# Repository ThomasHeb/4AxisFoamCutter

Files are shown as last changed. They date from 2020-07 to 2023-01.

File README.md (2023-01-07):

## What is new?
- Shared firmware with LaserCutter
  - tool is synchronized with grbl line execution
  - hotwire.cpp/.h is integrated in common tool.cpp/.h 
  - checkout [LaserCutter/Firmware](https://github.com/ThomasHeb/2AxisLaserCutter/tree/main/03_Firmware) for more insides
- Removed source for library modification, use provided libraries instead
- Rotary knob improved (no library needed)
- Libraries for Arduino can be downloaded directly from here (solving some issues with library updateds and conflicts with grbl)
- Added blockdiagrams for setup with Ramps 1.4 / Ramps 1.6
- Added selection guide for hotwire and power supply
- Fans are optional, if not connected, Pin 10 do not need to be cutted
- Simple postprocessor integrated in SketchUp tool Foamcutter.rb 

## What is coming next?
- Please let me know, if you have ideas or need improvements

# 4AxisFoamCutter

Arduino based CNC foam cutter with display and SD-Card.
Ruby Script for SketchUp Make 2017 to generate gcode.
Swift base post processing 

My goal was to build a foam based semi scale glider. So a lot of segments and very accurate working would have been necessary. This brought me to the idea to design the glider in SketchUp and build a 4 axis foam cutter.

The base idea ist very simple. Four independent linear axis with NEMA 17 stepper and belts. This simple system is satisfying,  because the accuracy of the belt and stepper is better than the impact of the hot wire, it's temperature and feed speed and almost no force is required to cut the foam. The only mechanical topic is to keep the hot wire stretched. Therefore I found a very good idea here on GitHub with retractable reels.

For controlling the four axis I found a solutions based on grbl 8c2 in combination with some Windows bases UIs and gcode sender. For generating the wing profiles I found some windows solutions or professional tools, but not free of charge, neither running on mac. For the fuselage I found only a professional tool. As I don't want a computer in my workshop, the gcode should be executed from a SD card, similar as my 3D printer does.  So I came to my project list:
- 4 independent axis 
- local display, SD card reader and control buttons
- Arduino based gcode handling, based on grbl 8c2 version adapted for foam cutting.
- fixed frame based on 2020 profiles, v-slot based linear actors (it is my first cnc machine, so there are much easier and better mechanical constructions, have a lock on https://www.rckeith.co.uk)
- only one power supply
- wing design with third party tools: 
  - WingHelper (I have a licence), export of gcode is possible but post process is required, I use my own post processor in MacOS, see below.
  - https://www.youtube.com/watch?v=uWO8kMGxqGU, Java based wing designer, including post processor. Exported dat file needs to be renamed to gcode-file extension. hotwire needs to be switched on manually.
  - http://www.diyrcwings.com/app/, Online wing designer, including post processor and hotwire controller. Exported file extensio  needs to be changed to .gcode
- fuselage design with SketchUp, therefore I wrote a small tool to generate gcode, see below
- post processing to adapt gcode to machine geometry for MacOS and combine multible jobs, see below

# Resources
Many thanks to all the guys giving me grad inspirations with their projects
- [rcKeith, Hot wire cutter](https://www.rckeith.co.uk/cnc-hot-wire-foam-cutter/)
- [4 axis foam cutter](https://github.com/rahulsarchive/4AxisFoamCutter)
- [4 axis foam hotwire cutter](https://www.rcgroups.com/forums/showthread.php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)

# Videos
- [Mechanic](https://youtu.be/zKdzEoycaa4)
- [Hardware](https://youtu.be/xaXfXsz1NG8)
- [Firmware](https://youtu.be/fht_X7mQ-qg)
- [Functions](https://youtu.be/SWv79BavgKs)
- [Working with SketchUp Part 1](https://youtu.be/MZSXp2stBLk)
- [Working with SketchUp Part 2](https://youtu.be/SIh3zpsxGX4)
- [Working with SketchUp Part 3](https://youtu.be/uU0HhuviuLE)
- [Working with SketchUp Part 4](https://youtu.be/WJ8nHyDqIhs)
- [Post processing Basics](https://youtu.be/D0ZCudA9wv8)
- [Post processing merging shapes](https://youtu.be/Z-096iua6jk)
- [Feed speed optimization with preprocessor](https://youtu.be/2PEHMFtozhw)
- [Post processing code insides Part 1](https://youtu.be/n6ZeKAKcKlE)
- [Post processing code insides Part 2](https://youtu.be/POwDu0zc9eI)

# Mechanics
- 4x linear v-slot actuator with NEMA 17
- 2020 profiles, screws, nuts
- nichrome wire
- 2-4x retractable reel 

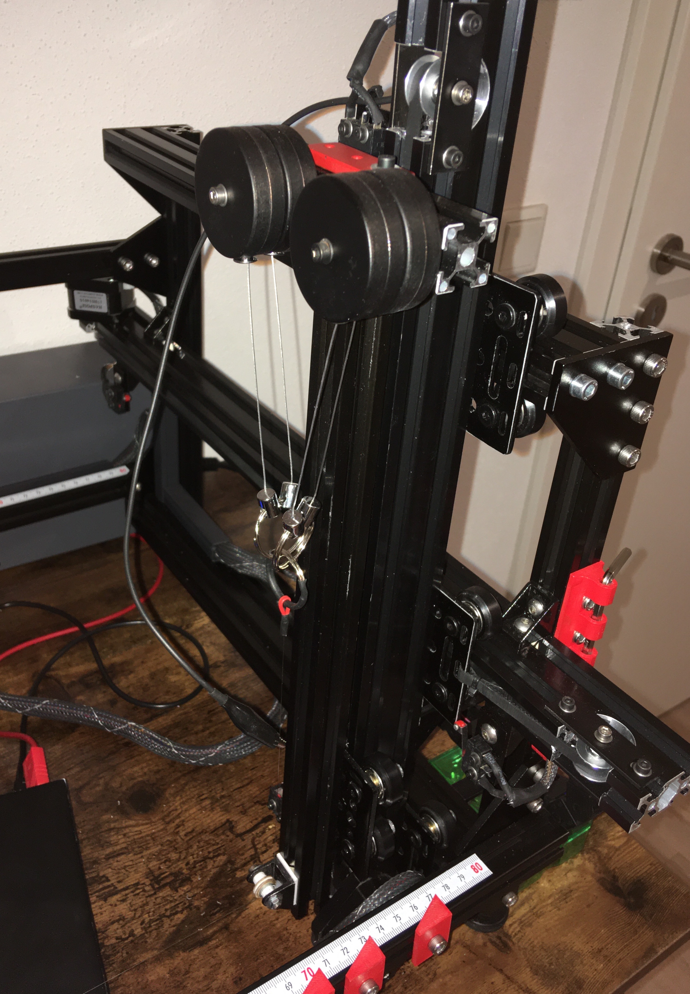
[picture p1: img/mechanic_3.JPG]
mechanic_3

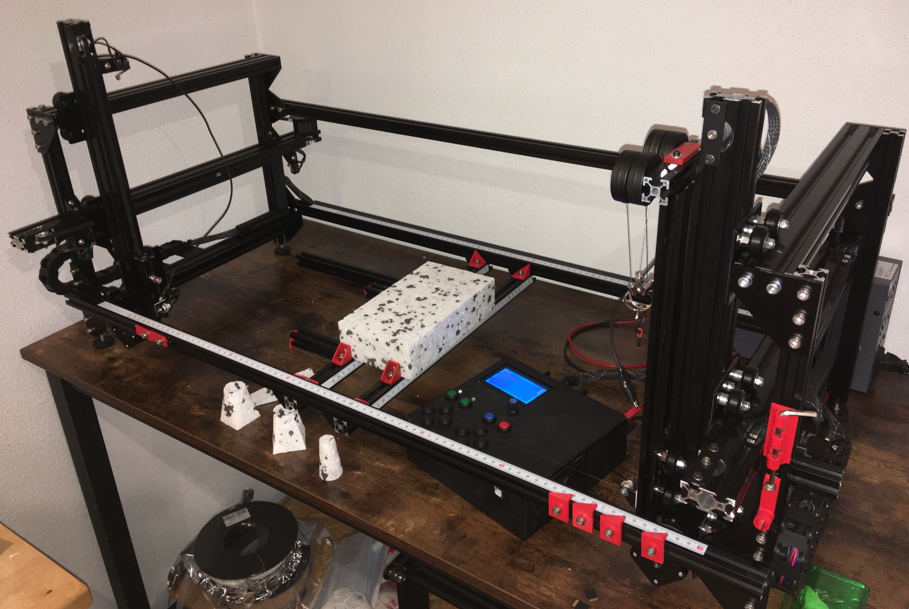
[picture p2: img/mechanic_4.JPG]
mechanic_4


[Video: Mechanic](https://youtu.be/zKdzEoycaa4)

# Hardware
- Arduino Mega 2560
- 128x64 LCD Display / SD card reader from RepRap with connector to Ramps 1.4 or 1.6
- Ramps 1.4 or 1.6
- 4x stepper driver A4988 (on E0, E1, Y, Z socket 0f ramps)
- 8x micro switch NC as limit switch
- 4x 100nF capacitor
- 12 buttons NO
- 2x LED + resistor 2k2
- DC-DC converter (in: > 30V, out 12V, app. 2A), not for Ramps 1.6
- optional: fans 12V
- wire / connector

Most of it is plugged together straight forward. A detailed list is included in the foamcutter.ino file.

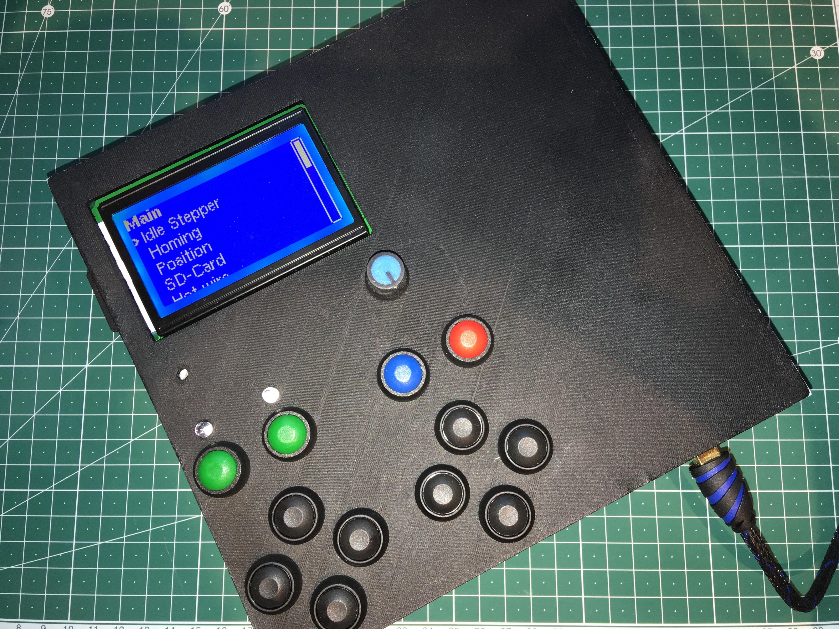
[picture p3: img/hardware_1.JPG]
hardware_1

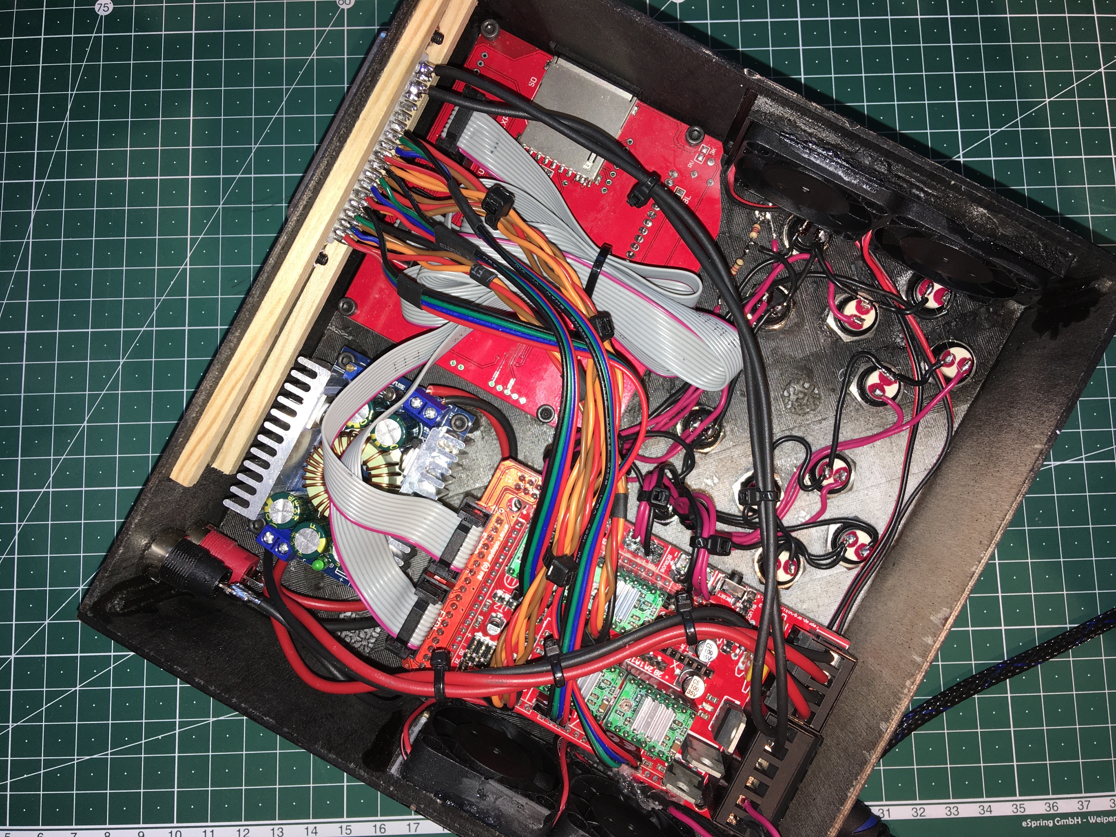
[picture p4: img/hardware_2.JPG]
hardware_2


### Blockdiagram for Ramps 1.4
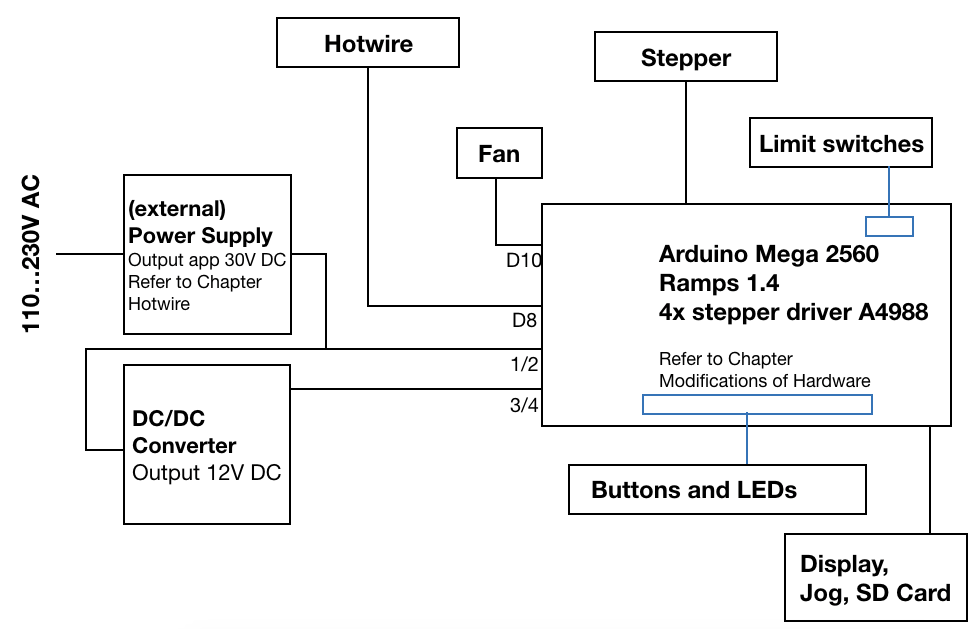
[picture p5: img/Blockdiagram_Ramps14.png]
blockdiagram_ramps14


A power supply is used with up to max 35V (limit of on board MOSFET on the Ramps) to supply the hotwire and the DC/DC converter. Refer to chapter Hotwire for voltage / power adjustment and selection of the right power supply.
The DC/DC converter supplys 12V DC to the Ramps, display, stepper and Arduino. I would not recommend more than 12V DC, because on the Arduino a linear voltage regulator is used to generate 5V DC and this can be easily over powered / heated, when input voltage is to high.
App. 30W are needed for Ramps, display, stepper and Arduino. In addition required power for the fans. I am using this [DC/DC converter](https://www.amazon.de/gp/product/B00HV4EPG8/ref=ppx_yo_dt_b_asin_title_o01_s01?ie=UTF8&psc=1), powering 4 small fans.
To select the right power supply, you need to keep estimate the power for the hotwire (see chapter Hotwire), power for Arduino, Display,... (app 30W) and the fans (20W for the small ones I am using), see chapter Power supply.
In my setup, nothing is getting hot, so I do not switch the fans on.... you do not really need fans.
Please check your power supply, if cooling is required. Please keep all standards and safety topics in mind, when handling with high voltage on power supply, best is to contact an authorised specialist.
A detailed list of all connections/wiring is included in the foamcutter.ino file.

Advantage:
- separate voltage for hotwire, helps to select best resistance wire, see chapter Hotwire. Especially with a small diameter: Higher hotwire voltage allows to have less current in the hotwire, select thiner wires with a higher wire resistance.

Disadvantage:
- additional hardware (DC/DC converter) needed, app 10 EUR 

### Blockdiagram for Ramps 1.6
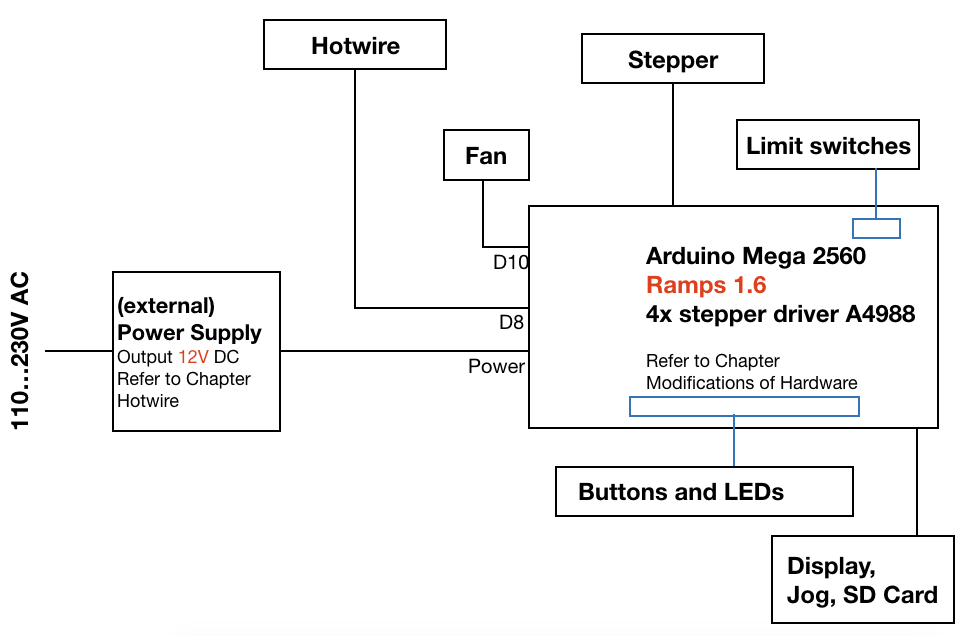
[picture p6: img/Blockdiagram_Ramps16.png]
blockdiagram_ramps16


A power supply with 12V DC output is used, because on the Arduino a linear voltage regulator is used to generate 5V DC and this can be easily over powered / heated, when input voltage is to high.
App. 30W are needed for Ramps, display, stepper and Arduino. In addition required power for the fans and the hotwire (see chapter Hotwire and Power supply).
I did not build a version with Ramps 1.6, but checking all the data sheets and diagrams, there should be no fan required for additional cooling of the Ramps board itself.
Please check your power supply, if cooling is required. Please keep all standards and safety topics in mind, when handling with high voltage on power supply, best is to contact an authorised specialist.
A detailed list of all connections/wiring is included in the foamcutter.ino file.

Advantage:
- no DC/DC converter is needed
- less wiring

Disadvantage:
- lower voltage for hotwire requires higher current  to achieve power for cutting. hotwire is getting thicker.

### Other Boards
Other boards may works, as long as they are based on the same or similar pin connection as the Ramps does. See Issues and search for MKS Board.

### Hotwire
Selecting the right hotwire is a bit tricky
I am cutting XPS foam with a very slow feed rate (100mm/min) for good results.
On my machine I have 20 W/m (watt per meter) to achieve good results. For calculation I would recommend to use 25 W/m (fine tuning can be done in power setting parameter).

Get the length L of your hotwire. Keep in mind that you have diagonal traveling of the hotwire, so the wire length is more than the machine width.
Get the Input voltage Ui for the hotwire (Ramps 1.4: app 30V (max 35V) / Ramps 1.6: 12V)
Calculate the total wire resistance Rtotal and the wire resistance per feet Rf

- Ptotal = L x 25 W/m
- Rtotal = Ui x Ui / Ptotal
- Rf = Rtotal / (L (in m) x 3,28)

The higher the input voltage Ui is, the higher is Rf, the lower the current through the wire and the MOSFET on the ramps. the MOSFET will stay cooler and most important, you can select thiner wires.
Now you can find the best fitting wire by checking the wire resistance per feet (Ohm/feet).

Example:
Total Hotwire length L = 0,9m. power supply works with output voltage of 30V (= Ui).
Ptotal = 0,9 x 25W/m = 22,5 W
Rtotal = 30 x 30 / 22,5 = 40 Ohm
Rf = 40 / (0,9 x 3,28) = 13 Ohm per feet
I would go for 
Kanthal A1 32G with 13,1 Ohm/feet [Link](https://www.amazon.com/-/de/dp/B07CHTFJ3J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)

Due to the calculation with 25W/m you will need to reduce power setting parameter for hotwire a bit to app 90…90%

Next step is to fine tune all your settings
- Go to the hotwire menu , select manual and start with a low power setting.
- Put some foam on it... the foam should not be cut.
- increase power setting until the foam is cut without putting force/weight on it. this is the setting for slow cutting speed (app 100 mm/min). Check out the [video](https://github.com/ThomasHeb/4AxisFoamCutter/files/5382446/IMG_4588.mov.zip).
- Put this setting into the parameter ($5 = feed speed and $27 = hotwire power is stored automatically from your last manual setting).

If your wire is not getting hot enough:
- increase input voltage (only with ramps 1.4: 28V >>> 30V)
- reduce wire length (put the crocodile connections closer together)
- chose a wire with a lower resistance .... thicker wire ;(

If your wire is getting much too hot / cutting is starting below 50% powersetting:
- there is no urgent need to change something
- reduce the voltage a bit. don't go below 10V to have enough power for the stepper
- increase wire length
- choose a wire with higher resistance >>> smaller diameter ;)

Start fine-tuning again until you are happy with the result.

### Power Supply
Selecting the right power supply is mainly based on four factors
- input voltage, select this according your region and local 
- choosing a power supply to integrate in the foam cutter or as a separate power supply (i.e. laboratory power supply)
- output voltage 12V DC or up to 35V DC. I would not recommend to use more than 60V DC because of risk of electrical shock)
- required power: 30W for Arduino, Display, Stepper + Fans (I use small 12V DC fans with total 20W) + hotwire Ptotal (see chapter Hotwire)

Please keep all standards and safety topics in mind, when handling with high voltage on power supply, best is to contact an authorised specialist.

### Operation without buttons, leds and limit switches (minimum operation setup)
There are some sets available for 3D printer, including Arduino Mega, Ramps 1.4, 128x64 Display with SD card reader and stepper driver 4988. The firmware can be configured to operate especially with this hardware setup, without buttons, led and limit switches. The usability is limited, but almost no soldering is needed.
To use this setup, simply skip all steps related to limit switches, buttons and leds. the local button on the display is used as back button, all other operations can be handled with the jog.
- set USE_LIMIT_SWITCHES to 0 in config.h to disable the limit switches 
- set USE_BUTTONS to 0 in config.h to disable the buttons and leds 

### Modifications of Hardware:
- cut-off Arduino PIN 10 on Ramps (just cut of the pin-header on the Ramps) (not required if no fan is connected) 
- connect Arduino Pin 7 on Ramps to Socket off pin 10 (not required if no fan is connected) 
- to reduce EMC connect 100 nF between S and - close to Ramps for limit switches / end stops
- to reduce EMC connect 100 nF between D63 and GND directly on Ramps pin header for AUX-2 (not required if stopp button is close to ramps) 

### How to start:
The Arduino and the Ramps board are working without the stepper driver or motors or buttons,…. so only the limit switches should be disabled by setting 4 jumpers to the S and - Pin for X-/X+/Y-/Y+ an the Ramps. After downloading the firmware with the Arduino IDE, please use the Serial Monitor (Baudrate 115200) with the [grbl commands](https://github.com/gnea/grbl/wiki/Grbl-v1.1-Commands) to disable hard limits and homing cycle in the parameter. After testing all axis, SD card, …, you can activate the limit switches (hard limits) and the homing cycle again. If you are not disabling the limit switches, you may get a hard error, which blocks all communication to the Arduino (not required, if USE_LIMIT_SWITCHES is set to 0). After that you should 
- connect the display to the Ramps
- connect the Arduino with the USB
- load the firmware and check if you get a welcome screen
- add the buttons and LEDs to the Ramps (not required, if USE_BUTTONS is set to 0)
- calculate the steps per mm and set the microstepps according with the jumpers (I use belt and pully with 80 steps / mm) 
- add the stepper driver to the Ramps
- adjust the driver [link](https://www.makerguides.com/a4988-stepper-motor-driver-arduino-tutorial/)
- connect 12V DC to Ramps 3/4
- add a stepper motor and test operation

[Video: Hardware](https://youtu.be/xaXfXsz1NG8)

# Firmware
The firmware is based on the grbl version 8c2 modified for foam cutter, a modified version of U8G2 library for the display and SdFat with no changes.

Links to the original 
- [grbl 8c2 foam](https://www.rcgroups.com/forums/showthread.php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)
- [U8G2 Lib by Oli Kraus, tested with version 2.27.6](https://github.com/olikraus/u8g2)
- [SdFat by Bill Greiman, tested with version 1.2.3](https://github.com/greiman/SdFat)

Many thanks to you, for writing and sharing this fantastic code.
The firmware is a common project with [2 Axis Laser Cutter](https://github.com/ThomasHeb/2AxisLaserCutter).
Please use defines in config.h to select the right funtionality.

### How to install:
- Download the foamcutter firmware
- Download the libraries directly from this github (recommended):
  /03_Firmware/libraries and store in your ../Arduino/libraries/ folder (prefered, because updates of the original libraries may cause problems with grbl)
- Select Version FOAM_CUTTER in config.h

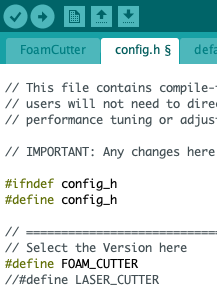
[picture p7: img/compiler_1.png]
compiler_1
  
  
### Changes within the library U8G2 - only for information:
Grbl uses almost all resources of the Arduino to control the stepper within an accurate timing. So the standard approach of Arduino is not working any more, because some resources are not available anymore for the Arduino framework. Within the U8G2 I use a software driven SPI on pin D50 to D52. The only thing I needed to change, was the required delay within the SPI. Therefore I changed the delay function to the grbl supported delay function.

### LCD, SD card and buttons, ….
The LCD display and the buttons are controlled inside the lcd.h and lcd.cpp. Buttons are read within the lcd_process(), from where all processing functions of the sub menus are called.
Functions within the sub menus, which are related to cnc functionality are called as if they would have been called via UART/USB. So you will get an ok over the UART/USB for a local called cnc command, too. The firmware can still be controlled with gcode sender tools via the UART/USB.
SD card is processed inside lcd.cpp and lcd_process(), too. Processing of the SD card is handled with a state machine, which reads the selected file char by char, similar as reading the UART. 
During processing a file from SD card, buttons are ignored, operation can only be stopped with an IRQ of the limit switches or the e-stop.
Fan can only be controlled locally on the display. Hotwire can be controlled via the display and with the gcode commands M3/4 for on and M5 for off and Sxxx (0…100) for regulating the power in %.

Please have a lock at the parameters (command $$ over Serial Monitor)

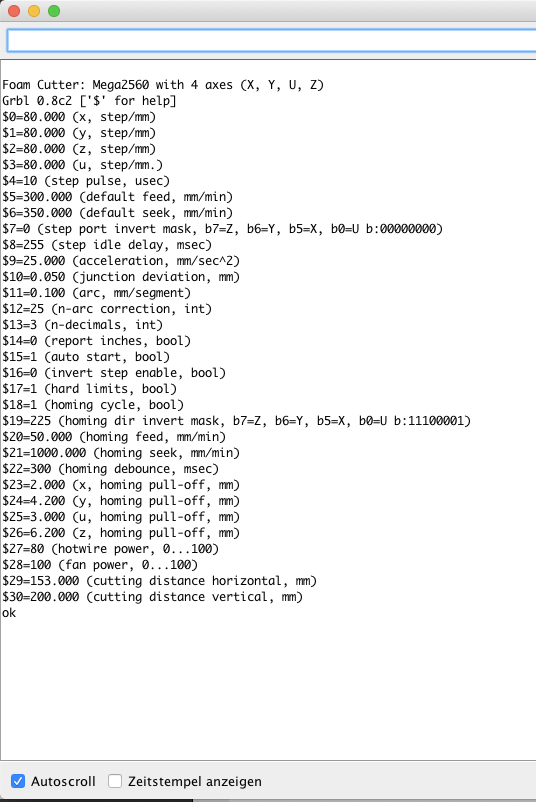
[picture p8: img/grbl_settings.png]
grbl settings


[Video Firmware](https://youtu.be/fht_X7mQ-qg)

### Functions on local display / buttons
- e-stop: IRQ based local stop, this does not match the requirements of any safety standard (not available, if USE_BUTTONS is set to 0)
- Idle stepper
- Homing (not available, if USE_BUTTONS is set to 0)
  - homing including pull-off
  - set current position as new pull off position: This function is used to travel from limit switches to machine zero position. Adjust the position with the position menu
- Position
  - adjust each axis independent
  - set or travel to a temporary home position
  - set or travel to a temporary zero position
  - 8 buttons to control the movements (not available, if USE_BUTTONS is set to 0)
  - switch speed between feed and homing seek for fast traveling (selected homing seek speed is indicated by LED
- SD-Card
  - read file list from SD-Card (only with defined file extensions (config.h), only from root directory, keep filenames short)
  - valid gcode file extensions: .nc, .gcode (you may change the file extension to oneof these)
  - execute a file from the SD-Card
  - visualise the progress (bytes read and send to gcode processing, not bytes really executed)
- Hotwire
  - switch on/off or change the power in %. New value is stored in the eeprom
  - switch on/off with button (not available, if USE_BUTTONS is set to 0)
  - indicate status with LED
- Feed speed 
  - select the feed speed
  - new value is stored in the eeprom
  - if gcode includes feed rates, gcode values are used.
  - adjust in big steps with Y- / Y+ buttons (not available, if USE_BUTTONS is set to 0)
- Slicing (previous function name: Cutting)
  - this functions allows horizontal or vertical slicing w/o gcode
  - select the slicing direction with the 8 buttons for the axis (not available, if USE_BUTTONS is set to 0, direction is selected with jog)
  - define the maximum x/y travel for slicing (use position menue)
  - executes a cut by preheating the hotwire for 5 seconds
  - move back to starting position of the slice with seek-speed
- Fan
  - switch on/off or change the power in %. New value is stored in the eeprom
- The firmware can still be controlled with gcode sender tools via the UART/USB 

- [Video: Functions](https://youtu.be/SWv79BavgKs)

### How to start:
Please refer to grbl documentation for parameter settings and first steps. A good point to start is to:
- disable limit switches and homing cycle (not required, if USE_LIMIT_SWITCHES is set to 0)
- set the steps per mm for each axis
- check the direction and adjust with "step port invert mask"
- check travel distances and optimize
- activate homing cycle and check directions and adjust with "homing dir invert mask" (not required, if USE_LIMIT_SWITCHES is set to 0)
- a good setting to start is feedrate 300 mm/min, hotwire 80% on 30V DC for 75 cm hotwire

# Working with SketchUp

I use SketchUp for generating the stl-files for my 3D printed parts. I would love to use the easy handling for creating fuselages. I searched the web and found only one hotwire related tool, which is not supported any more. so I decided to write a small tool by myself. This allowas you to generare G90 (abolute positioning) coordinates of combinded edges. Currently I use only linear extrapolation in combination with my post processor. The results are good.

### What you need
- SketchUp (I am Using SketchUp Make 2017)
- Ruby Code Editor
- CurviLoft
- Download foamcutter.rb from the code section

### Functionality and usage of foamcutter.rb
Open the ruby code editor first and load and execute the foamcutter.rb. This adds 4 menus to the PlugIn menu. 
- FoamCutter Settings: you can define some general settings, like inch/mm, used decimals.
- FoamCutter Import how-file: Import profiles from Wing Helper
- FoamCutter Tool: Generates gcode for 2 paths and exports it. The paths it self use the green (x and u) and blue (y and z) axis. Positioning along the red axis does not matter. See tutorial video "Working with SketchUp Part 1-3"
- FoamCutter Tool PP: Generates gcode for the left and the right axis of the foamcutter, this includes a simple post processing. See tutorial video "Working with SketchUp Part 4"

The algorithm searches all related points to an edge. It follows two routes
### 1: go up first (Y/Z +)
### 2: go back first (X/U -)
It uses all edges only once. If you reach a dead end, you may use the third dimension (supporting path) do open up new paths/edges - please keep the rules in mind.

Both paths should have the same number of points and edges. To go for that with more complex objects, it is a good way to use CurviLoft
- create your objects
- use CurviLoft to generate the surface/area between the objects. 
- select to show the related edges between the objects (connection lines)
- split these connection lines (ungroup)
- select and group the objects (otherwise the object is not splittet in points)
- delete the connection lines
- use foamcutter tool
- select first and second edge
- save the file
- do the post processing if required

### Check out the tutorial video
- [Working with SketchUp Part 1](https://youtu.be/MZSXp2stBLk)
- [Working with SketchUp Part 2](https://youtu.be/SIh3zpsxGX4)
- [Working with SketchUp Part 3](https://youtu.be/uU0HhuviuLE)
- [Working with SketchUp Part 4](https://youtu.be/WJ8nHyDqIhs)

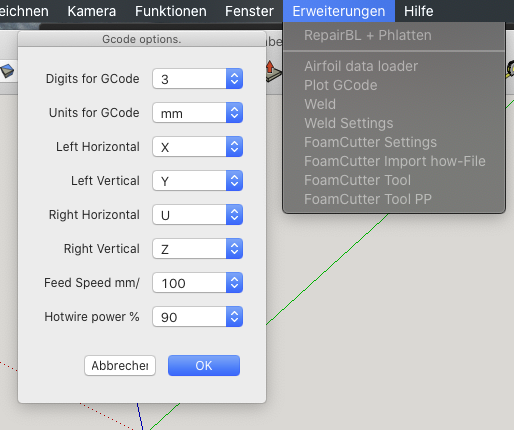
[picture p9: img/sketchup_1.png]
sketchup_1

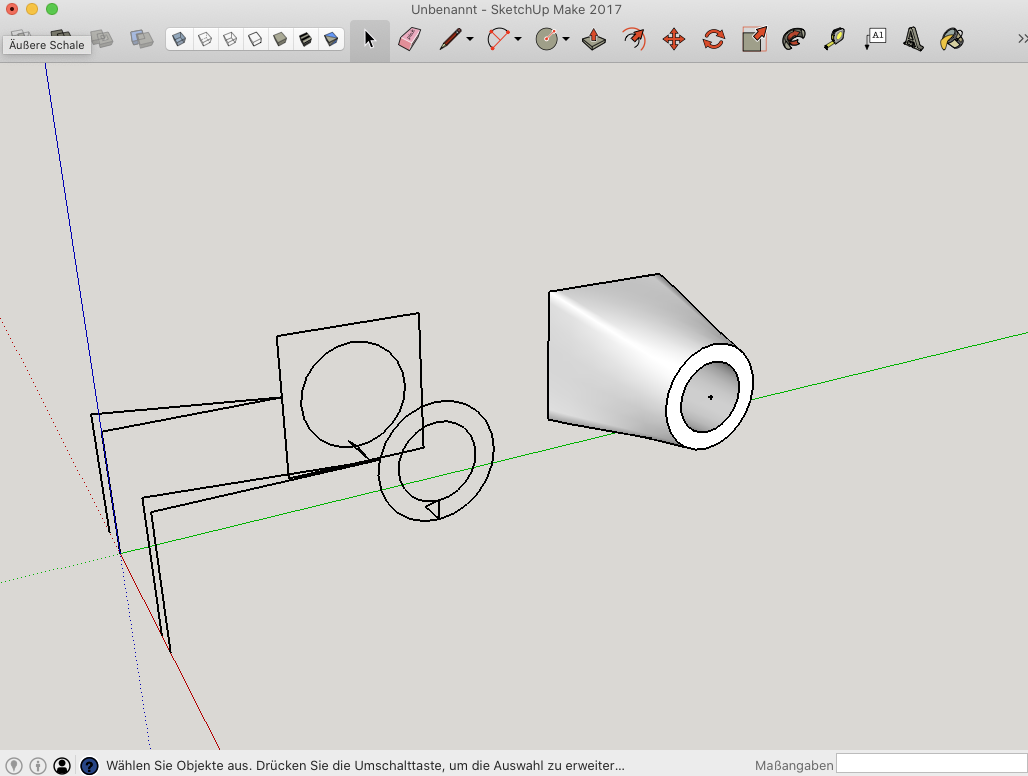
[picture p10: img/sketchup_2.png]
sketchup_2


# Post processing
Designing the shape of a wing or a fuselage requires in most times an additional step to tell the machine / foam cutter how to produce it. This step is called post processing. It allows you to generate machine executable or interpretable code (gcode) and add machine, tool and material specific information (hot wire temperature, travel speed, position of foam block, …). I wrote a pice of code, do adopt my SketchUp files and my WingHelper Designs to my foam cutter. The code is written in swift for macOS, but the basic ideas can be easily adopted to other languages. All post processing functions are bundled in the class FCalc (FCalc.swift). Interfacing is handled with key to access the values and the labels/descriptions to the values. The values itself are exchanged as Strings, because most of them are changed by user, so all type checking stuff is integrated in FCalc, too. Detailed interface description is available in FCalc.swift.

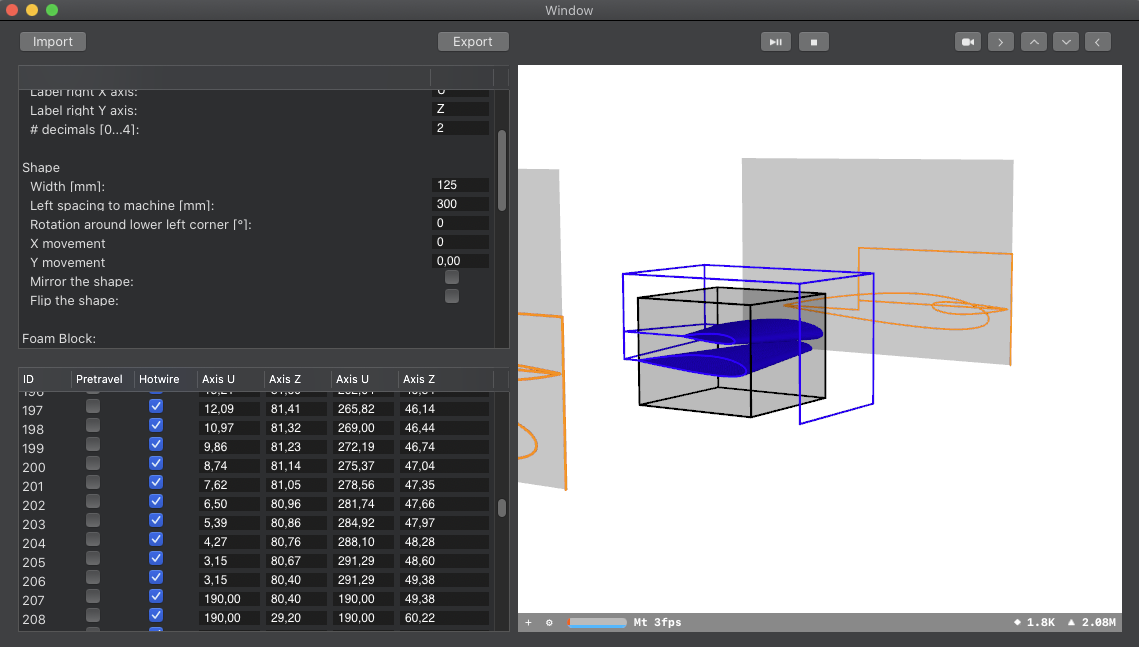
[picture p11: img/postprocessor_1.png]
postprocessor_1


### Overview of functions
- Import shapes from gcode, nc, SkechUp foamcutter.rb, Winghelper how, fcf-projects
- Export to gcode
- Load/Save projects as fcf file
- Move and rotate and mirror the shape 
- Move and rotate the foam block
- Calculates the movement of the axis
- Speed optimisation, to keep average speed at the edges of the shape close to target feed speed
- Merging of different shapes into one cutting job
- 3D preview and simulation of axis, shape and foam block

### Check out the tutorial video
- [Basics](https://youtu.be/D0ZCudA9wv8)
- [Merging shapes](https://youtu.be/Z-096iua6jk)

### Settings
- All settings have a unique ID (see SettingsTableKey for all values) for access
- Reading a setting:
  - dataTypeForKey(_ key: SettingsTableKey) -> DataType              
    the Datatype of the setting for correct visualisation/layout
  - labelForKey(_ key: SettingsTableKey) -> String                   
    the label for the setting
  - valueForKey(_ key: SettingsTableKey) -> String                   
    the value itself for the key as formatted string
- Writing:
  - isEditableForKey(_ key: SettingsTableKey) -> Bool                
    indicates wheather this type is editable
  - isValueValid(_ key: SettingsTableKey, value: String?) -> Bool    
    a string can be tested, if it is acceptable for this setting
  - valueForKey(_ key: SettingsTableKey, value: String?)             
    writes a string to the setting
- Usage: Generate an array of SettingsTableKey-values to be displayed and catch the content with the functions above
- All is handled with strings, so no need of type conversion

### Import a file / export GCode
- Supported filetypes;
  - gcode, nc: simple gcode wit G00/G0, G01, G1, G90, G91, ...
  - how: Winghelper ICE export with absolute coordinates
  - fcf: Foam Cuter File (project) previously saved
  - importShapeFromFile(_ file: String) -> Int       
    =  0 if ok / != 0 if not ok
- Save a file in gcode format
  exportGCodeToFile(_ file: String) -> Int         
  =  0 if ok / != 0 if not ok

###  Callbacks (FCalcCallback):
- updateSettingsTableView()  
  called, wenn the table for the settings needs to be updated
- updatePositionsTableView(_ atIndex: Int?)                                 
  called, wenn the table for the positions needs to be updated
- updatePreview(_ node: SCNNode)  
  called, whenn the Graph is updated, check if Node is already linked

###  Changing Values / Coordinates:
- optional, see FCalc.swift

###  Videos explaining some code insides:
- [Part 1](https://youtu.be/n6ZeKAKcKlE)
- [Part 2](https://youtu.be/POwDu0zc9eI)

# Samples
See folder 99_sample in the code section:
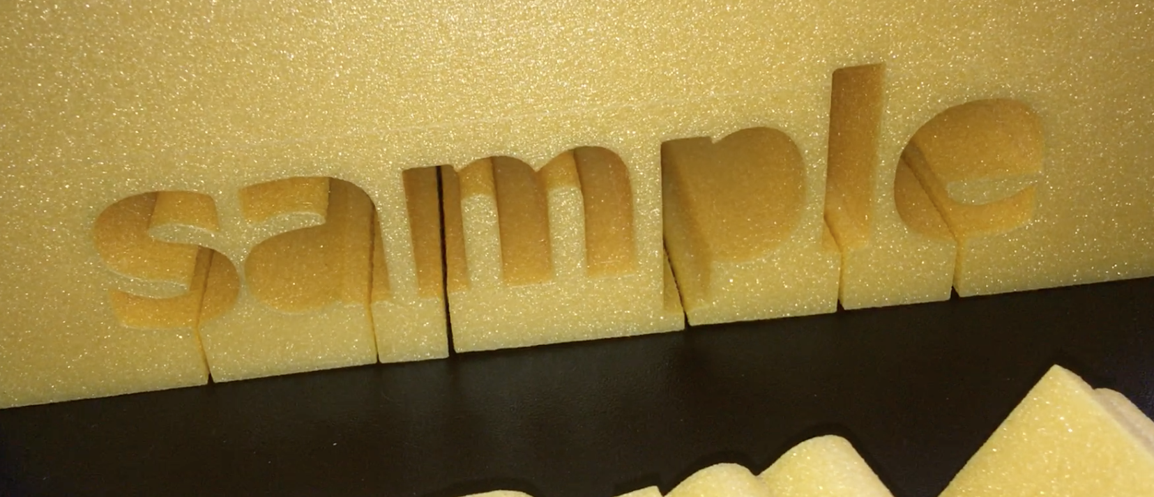
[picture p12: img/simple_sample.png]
simple_sample

- sample_1.gcode is the export file from foamcutter.rb (SketchUp) 
- sample_2.gcode header and commandes were modified manually with text-editor
- sample_pp.gcode is generated with post processor

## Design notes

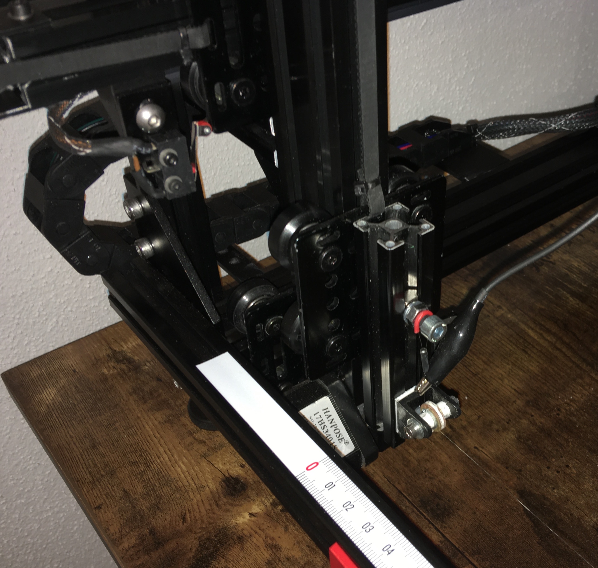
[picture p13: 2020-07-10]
img/mechanic_2.JPG

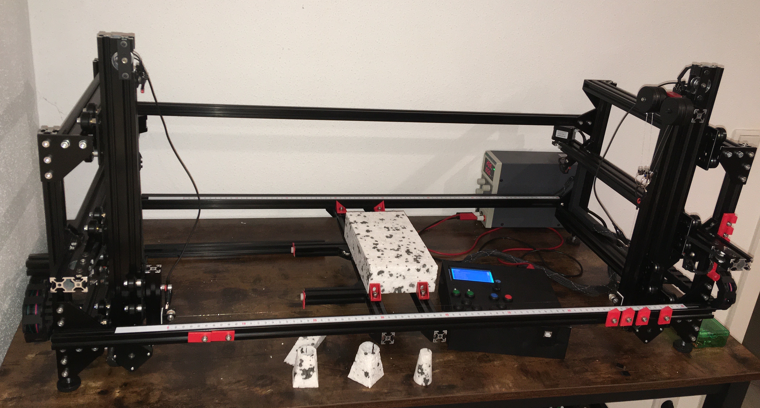
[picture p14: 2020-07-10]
img/mechanic_1.JPG

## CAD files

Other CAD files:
01_Mechanic/Foam-Cutter.skp
04_SketchUp/Example_Tower/Tower.skp

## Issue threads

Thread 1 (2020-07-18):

Inverse Time Feed Mode not working

ThomasHeb, 2020-07-18:
Inverse Time Feed Mode G93 not working. Machine moves very slow. Mainly used by DevFoam

ThomasHeb, 2020-07-18:
Updated planner.cpp / void plan_buffer_line(…
…
  if (!invert_feed_rate) {
    inverse_minute = feed_rate * inverse_millimeters;
  }
  else {
    inverse_minute = /* 1.0 / if feedrate is G93 it is already inverted!!!*/ feed_rate;
  }

Inverse Time Feed Mode G93 is working correctly

Closed 2020-07-18.

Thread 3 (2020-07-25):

Post processor: Merge of shapes

ThomasHeb, 2020-07-25:
To generate more efficient gcode programmes, shapes from different sources should be combinable within one cutting job.
- merge different files
- move one shapes independent from other
- add lines
- delete lines
- modify lines

ThomasHeb, 2020-07-25:
Implemented. Import function always keeps the current design in green color inside the preview, ready to be merged, but not effected by the movements / settings. In addition complete projects can be imported (fcf-files). With a merge the shapes are combined to one common shape, "left spacing from shape to machine" is kept from the last design, rotation, flip, mirror, x and y movement of both shapes are set to 0 (never the less, the shapes are combined as they were positioned/rotated), foam dimensions of the last shape are kept. The last added shape is processed first, so build up your common shapes from the bottom to the top.
traveling between the shapes should be optimise with „delete/insert line“ functions and modification of the position of single points (use simulation inside the preview).

Closed 2020-07-25.

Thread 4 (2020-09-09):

Error when compiling for Arduino

ThomasHeb, 2020-09-09:
Hallo Thomas, bekomme beim Kompilieren einige Fehlermeldungen, könntest du mir da bitte weiterhelfen?
Danke!

Mehrere Bibliotheken wurden für "U8x8lib.h" gefunden
 Benutzt: C:\Users\Jetpilot\Documents\Arduino\libraries\U8x8libr
 Nicht benutzt: C:\Users\Peter\Documents\Arduino\libraries\Lib_8UG2
 Nicht benutzt: C:\Users\Peter\Documents\Arduino\libraries\U8g2
lcd.cpp:7:10: fatal error: SdFat.h: No such file or directory
 #include "SdFat.h"
          ^~~~~~~~~
compilation terminated.
exit status 1
SdFat.h: No such file or directory

ThomasHeb, 2020-09-09:
Bitte prüfe, dass nur eine U8G2 Lib installiert ist.
Öffne hierzu in Arduino unter Werkzeuge/Bibliotheken verwalten...
Suche hier nach U8G2.
Prüfe ob mehrere Libs installiert sind.
Wenn ja, lösche diese in deinen Lib Verzeichnissen (C:\Users\Peter\Documents\Arduino\libraries\ bzw C:\Users\Jetpilot\Documents\Arduino\libraries), am besten löscht du alle U8G2 Libs
Installiere die U8G2 Lib neu (U8g2 by oliver Version 2.27.6 siehe Screenshot
https://github.com/olikraus/u8g2
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

Installiere die SDdFat - Adafruit Fork by Bill Greiman Version 1.2.3 Lib, siehe Screenshot
https://github.com/greiman/SdFat
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

Einbinden einer Lib in Arduino:
Lade die Lib als Zip-Datei von Github
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

Unter Arduino/Sketch/Bibliothek/.ZIP-Bibliothek hinzufügen... wählst du die ZIP Datei aus.
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

Die Libs erscheinen dann in den Arduino-Lib Verzeichnis
Hier musst du auch die U8x8lib.h and U8x8Lib.cpp (download von hier aus dem Projekt) im Verzeichnis U8G2 tauschen.
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

Campilot, 2020-09-10:
Danke Thomas!
Alle Fehler bis auf einen sind gefixt - hab aber noch immer den LCD Error

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

Campilot, 2020-09-10:
@ThomasHeb
 U8x8lib.h and U8x8Lib.cpp hab ich natürlich ersetzt :)

ThomasHeb, 2020-09-10:
Hallo,

bei dem Stand "fatal error: lcd.h:  no such file...." fehlte wirklich die lcd.h und die lcd.cpp aus meinem Source-Code. Sieht man auch, wenn man deine beiden Screenshots vergleicht... da fehlt in der Arduino IDE die Lasche mit lcd.h und lcd.cpp.
Die Fehler bzw das Hängenbleiben hängt mit der Installation der U8G2 Lib zusammen.
Ich würde vorschlagen, dass Du einfach meinen Lib-Source 1:1 nimmst, liegt hier: https://github.com/ThomasHeb/4AxisFoamCutter/tree/master/03_Firmware/libraries . Nur die u8g2_font.c fehlt (Verzeichnis /libraries/U8g2/src/clib/), da > 25MB.

Schließe die Arduino IDE.
Bitte sichere die die u8g2_font.c aus deinem library Ordner.
Lösche die Libraries in deinem Ordner
Kopiere die beiden Libs von hier rein.
Füge die u8g2_font.c unter /libraries/U8g2/src/clib/ hinzu
Starte die Arduino IDE neu und kompiliere den Foamcutter.

ich wäre morgen Nachmittag auch gut zu erreichen.... glaube das ist nur ein banaler Fehler, der sich aber gut versteckt.

LG
Thomas

Campilot, 2020-09-11:
Hallo Thomas!

Zuerst mal vielen Dank für deine Unterstützung!!

Gute Nachricht, jetzt hat es funktioniert - anscheinend ist Oliver´s Lib korrupt?

Ich hab in den letzten Monaten 4 Foamcutter gebaut (hab auch viel Kontakt mit Keith Howlette) -  wenn du an der Mechanik interessiert bist, dann schick ich dir gerne einen Link zu meiner Dropbox - die meisten Teile sind 3d gedruckt und Antrieb über Riemen mit V-Slot Rollen!

Nochmal Danke und LG

Peter

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

ThomasHeb, 2020-09-11:
Hallo Peter,

freut mich, dass es jetzt klappt. Ich werde in den nächsten Tagen noch ein Update machen, um die Verfahrgeschwindigkeit auch lokal direkt an einer Taste umzuschalten. Du kannst Dir ja einen Notifier in GitHub legen, dann bekommst du eine Info, wenn ich die Firmware hochlade.
Gib mir auch gerne bescheid, wenn du weitere Funktionen brauchst.

An der Hardware bin ich auf jeden Fall interessiert.

Brauchst du die Libs noch (https://github.com/ThomasHeb/4AxisFoamCutter/tree/master/03_Firmware/libraries)?
Wenn nein, würde ich diese hier löschen, da ja nicht von mir geschrieben.

LG
Thomas

Campilot, 2020-09-11:
Hallo Tom,

ja mich freut´s auch...aber so richtig :D

den Notifier check ich gleich!

Die Libs brauche ich nicht mehr, hab sie lokal bei mir am Rechner ;)

Ich kopiere bis Sonntag mal sämtliche Daten in einen Dropboxordner und schick dir dann die Einladung!

hier ein link zu meiner ersten Styro Cnc -> https://www.youtube.com/watch?v=LLoHfbii8cM&t=23s

da hab ich aber noch einige Dinge grundlegend verändert, speziell die Drahtführung (war bei V1 noch mit einer Feder gespannt)

LG

Peter

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

ThomasHeb, 2020-09-11:
Hallo Peter,
freut mich! Video habe ich geprüft, wenn du willst kann ich deine Mechanik / Videos auch gerne mit hier verlinken.
LG
Thomas

Closed 2020-09-11.

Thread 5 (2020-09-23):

Slight confusion with modifications and connections to ramps1.4 board

goos766, 2020-09-23:
https://ibb.co/88wLdn4 I am not sure if I understood your connection description correctly. Therefore, I am sending you this diagram to confirm that it is correct. I would be grateful if you could point out the errors in the diagram. I know that I mixed up a bit in the connections to the 100nf capacitors at the ends stops, because I didn't read it carefully. One more question, what should 100nf capacitors look like, what should I really look for? From what I've read, I conclude that I should solder one 100nf capacitor for each of the four ends tops, connecting the signal and ground. Can you provide details, so I don't make a mistake and burn the board when buying wrong parts, can you send a link? Is using an external MOSFET like in 3d printers incompatible with your firmware? The external MOSFET seems to keep the PWM functionality. I am asking you as an expert in this matter because I know little about it. You can answer me in German, Google will surely help me. I am very keen to get ahead with the project. My only regret is that I can't use your software, and I don't have programming skills to convert it to PC. It looks very interesting from your videos.

goos766, 2020-09-23:
Is using an external MOSFET like in 3d printers completely incompatible with your firmware? The external MOSFET seems to retain the PWM functionality. I am asking you as an expert in this matter because I do not know much about it.

ThomasHeb, 2020-09-27:
First of all, sorry for my late reply. I know that is frustrating, if a project get's sucked.

Your wiring has some errors.
- Stepper drivers are assigned correct
- capacitors on limit switches are correct, wiring see picture below
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
use a very small 0805 100nF capacitor and solder it from the bottom side of the ramps, directly between the pins (picture is not soldiers, but shows the first position, in addition solder the next 3 headers to the right lower side a cap, too. one 100nF for each limit switch line Signal (S) to GND (-) ... 4 Cs in total).
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
- buttons X/Y/U/Z arrangement is wrong, X/Y is the left side, U/Z the right side. See attached picture
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
- Cut of pin 10 and connection to pin 7 is not correct, see attached picture. please cut of only the pinheaded on pin 10 on the ramps board. no modification on the Arduino. Wiring between the pins as shown in the picture
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
- power supply / hotwire / fan connections are correct
- button wiring:
  - stop, back, speed, hotwire buttons are correct (ramps labels D48, but it is D40 in the Arduino)
  - X+/-, U+/- wiring are correct (button arrangement is not correct, see above)
  - swap Z+ and Z-
  - swap Y+ and Y-
  - please check the FoamCutter.ino for wiring the buttons
You can use an external MOSFET, but it is not required. If you have a power supply with app. 28... 30V you will have a current of app 0.5A for 80cm of hotwire. This is less than the stepper drivers will need. so you can connect the hotwire directly to the ramps. If you want to use an external MOSFET, you can grab pin 8 on the arduino to control the MOSFET. pin 8 is active high. I would recommend to use internal MOSFET, or if not possible. control your hotwire manual, by switching it on before cutting and off after cutting (i.e. some chargers for RC cars/planes have a hotwire function).
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

You are the second guy asking for a windows version of the post processor. If someone can do the user interface, I could support with a common/universal class file for the post processing functions.... let's see what happens in future...

goos766, 2020-09-29:
To begin with, I want to thank you very much for your effort to write such a wonderful description. For now, I am waiting for a few more parts that have been sent to me from China. At the moment I am designing my version of the foam cutter based on the rckeith.co.uk design. I will try to deal with electronics soon.

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

goos766, 2020-09-30:
I made corrections to the wiring diagram, I hope I have not missed anything
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

goos766, 2020-09-30:
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
My miniature version of the foam cutter controller

ThomasHeb, 2020-10-01:
Hi,

wiring looks much better. I only found Z-/Z+ to be swapped: Z- goes to D4, Z+ to D11.
I use two LEDs on D65 (Hotwire) and D66 (Speed). This indicates if the wire is on or if I switched to seek speed (positioning menu). But they are not a must.... you will see it, if the machine goes fast and you will smell it, if the wire is on ;P

It is a very good idea to include the button on the display in your design, If you have any wishes (placing a function like homing on it,...), let me know.

Please be aware, that you select most of the menus by pressing the rotary button. This needs some force, so everything has to be stable and should not tilt.

Overall this is an awesome design! Thanks for sharing.

goos766, 2020-10-02:
The case design is a cluster of models from thingiverse.com. As for the stability of the housing, I am going to add tabs for the screws. The button on the housing of the screen is the reset button, so I think I can select the homing function from the menu. If I have no problems with uploading the software. At the moment, I am still struggling with the mechanics of printing parts and selected the cheapest and best solutions, trying to maintain the functionality and rigidity of the structure.

ThomasHeb, 2020-10-03:
The tabs for screws are a very good idea. Maybe you can separate the green and the yellow button fields a bit and add a raised stabilizer between from top to bottom. Keep the two wires and connectors between displayboard and ramps in mind. I think it is very useful to have a connector between the electronics and the mechanics, so I added a sub-d connector to the housing (walls must be very stable in the area).

The outer design is very compact.... good job.

goos766, 2020-10-06:
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

goos766, 2020-10-07:
After uploading the firmware, I was surprised that the reset button on the screen does not work like on 3d printers. Now I know what you meant by saying that you could assign to this button a function other than its default function, which is reset.

ThomasHeb, 2020-10-07:
Hi Goos,

if you use the slicing menu, you select the cutting direction with the buttons.
Or use the jog for setting new max position (machine must be homed and positioned correctly to the max cutting position), or do a back travel.

So slicing makes only sense with the buttons (and the steppers). limit switches are not needed for slicing.

You can quickly define the onboard button as back button inside led.cpp, change
#define BTN_ONBOARD                   0x00000001
to
#define BTN_ONBOARD                   0x00000080

I would recommend to follow the next steps:
- connect the buttons
- connect one stepper driver and motor
- connect 12V DC to Ramps 3/4
- go to position menu and check if you can move this stepper with the -/+ buttons
this helps you to check, if buttons are wired correctly.

goos766, 2020-10-07:
I'm glad you answer me at all. I appreciate your willingness to help strangers. I am pleased with your every answer and your time devoted to dealing with my problems.
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
goos766, 2020-10-14:
More resistance means thinner cutting wire, or I get it wrong again. I currently have a 12v 30A power supply (at least this is what it says on the sticker), which in the past I was supposed to use for a 3d printer in the ramps 1.4 configuration in case it broke something inadvertently and I needed a quick replacement, but it did not happen so I have a new one / unused.

For now, I am trying to solder cables to use parts lying around unused for several years. The key idea here is to connect DuPont plugs with JST plugs, it could be done probably cheaper using a crimper, but in recent years I have bought a few crimping tools and never suitable for such small things. I have some female to female DuPont cables for which I did not find any use and some JST cables left after the ender 3 cabling modifications. I figured I wouldn't be spending my money again on something that would come in about 2-3 months if at all so I cut a few cables and solder them now.

ThomasHeb, 2020-10-14:
Hi Goos,

more resistance means thinner cutting wire, correct.... but if you go from 28V to 12V you need less resistance, to get the required power on the wire (32W = 28V x 1,4 A = 12V x 2,7A). This may lead to thicker cutting wire. My 12V recommendation is
https://www.amazon.com/-/de/dp/B07CHX4MMT/ref=psdc_495310_t2_B07CHSG169
Diameter is 0,64mm..... I remember, that's why I have chosen the proton with 0,2mm and played with the voltage, too.

I cutted all connectors, too and I am using standard pin connectors 2,54mm male/female as connectors. Glue them together and where needed some isolation ;)

I finished the test with the unmodified Ramps 1.4 board. Standard firmware without modifications:
You do not need to cut Pin 10 as long as you don't use a fan. Appending some screenshots. You see that the internal MOSFET stays very cool (10 minutes, ambient temp. 18°C, no fans active). So Ramp 1.4 and Ramp 1.6 will work. I would only recommend to add the Cs for EMC compensation.

28,5V / 0,9A: stepper + Hotwire
28,5V / 0,38A: stepper (10,83W)
Values are a bit different because of different ramps/arduino and because I did not do all parameter settings.

Less Voltage means higher current, because power consumption stays almost constant
25,6V / 0,42A: stepper (10,75W) ... only hotwire is not getting hot enough if  reduce more.

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

goos766, 2020-10-14:
ok. I took a step forward with all the stepper motors and their directions checked. Tomorrow and maybe even today endstops soldering. later ... ehh, what the hell, I will cut this pin 10, because without this fan I feel somehow insecure. I have to prepare for testing the cutting wire, because I do not have a power cable of the right length for this whole test to make sense.

ThomasHeb, 2020-10-15:
Hi Goos,

the resistance of the hotwire is measured directly on the hotwire. Between the points, where you connect the cables.... see picture.
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

Resistance is the base for choosing the right wire.
Connect everything. Go to the hotwire menu , select manual and start with a low power setting.
Put some foam on it... the foam should not be cut.
increase power setting until the foam is cut without putting fore on it. this is the setting for slow cutting speed (app 100 mm/min). Check out the video attached in the zip.
Put this setting into the parameter ($5 = feed speed and $27 = hotwire power is stored automatically from your last manual setting).

If your wire is not getting hot enough:
- increase input voltage (only with ramps 1.4: 28V >>> 30V)
- reduce wire length (put the crocodile connections closer together
- chose a wire with a lower resistance .... thicker wire ;(

If your wire is getting much too hot / cutting is starting below 50% powersetting:
- there is no urgent need to change something
- increase wire length
- choose a wire with higher resistance >>> smaller diameter ;)

I keep my fingers crossed for your fist cut!

[IMG_4588.mov.zip](https://github.com/ThomasHeb/4AxisFoamCutter/files/5382446/IMG_4588.mov.zip)

goos766, 2020-10-15:
So it seemed to me at the beginning. But after reading that the power cable also influences the resistance of the entire installation, I started to doubt a little where this resistance measurement should actually take place. Thanks for that clarification.

ThomasHeb, 2020-10-15:
Of course everything has an influence. But to get that baby working, you can focus on the major topics ;o)
Cables have less than 1% impact compared to the hotwire/resistive wire.

Closed 2020-10-21.

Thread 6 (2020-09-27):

Using a MKS Base v1. 4 Board

ThomasHeb, 2020-09-27:
Request from youtube.com
https://youtu.be/Z-096iua6jk

Kann ich mein altes board von meinem 3d Drucker verwenden?
Ich habe ein MKS Base v1. 4
Mit dem atmega2560
Und ich habe gerade grbl instaliert auf meinem board
Kann ich das display vom drucker mit sd card verwenden?

ThomasHeb, 2020-09-27:
Das MKS Base 1.4 Board sollte funktionieren.
Leider gibt es keinen Schaltplan, aber die Pinouts sehen gut aus.
Buttons, Limitswitches, LEDs, Display und SD-Karte (Reprap sollte hier gehen, aber die Graphik Version, siehe Bilder) und Stepper sollten passen (siehe Bilder im Anhang).
Ich habe am Ramps Board ein paar Modifikationen durchgeführt.
- Die Entstörkondensatoren für die Limit switches (Endschalter) kann man auch am MKS anbringen, siehe Bild im Anhang.
- Das durchtrennenden Arduino Pin 10 und verbinden auf Pin 7 am Ramps geht nicht. dies ist aber kein großes Problem, da nur der Fan (Lüfter) dahintersteckt. Bei mir wird da nichts heiss, also ist der Lüster noch nie gelaufen und zur Not kannst du einen Lüfter direkt an 5V oder 12V anschließen.
- Damit es nicht zu Problemen kommt, musst du in der Firmware ein paar kleine Anpassungen machen
  - Datei fan.cpp / fan_off():  Lösche Zeile: TCCR4A &= 0b11001111;
  - Datei fan.cpp / fan_init():  Lösche Zeile: SET_OUTPUT.... bis inkl. ICR4    = 255;
  - Datei fan.cpp / fan_run(...): Lösche Zeile TCCR4A |= (1 << COM4B1); und  OCR4B    = fan_data.pwr;
  - Damit greift der Fan nicht mehr auf die HW zu ;o)
- ODER du lässt die Modifikationen und schließt den Fan mal an E1/D7 an.... hier hat das MKS Board ein wenig mehr drauf als das Ramps, vielleicht klappt es
- Hotwire wird an Heat Bed/D8 angeschlossen
- Spannungsversorgung
  - es gibt zwei Anschlüsse. Bitte schließe das LCD Display an und Lade die Firmware. Trenne die USB Verbindung und schließe dann an einer Spannungsversorgung an. Wenn das Display leuchtet ist diese für die Versorgung vom Arduino-Teil und der Stepper-Motoren verantwortlich. Bitte hier 12VDC anlegen. Die andere ist für das Hotwire.

Wenn noch weitere Fragen sind, dann bitte einfach stellen.

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

ThomasHeb, 2020-09-28:
Anbei noch der link zum Display
https://www.amazon.de/Redrex-Vollgrafik-Display-Controller-3D-Drucker-Arduino/dp/B01LO20XGS
TFT Displays von MKS oder 4-Zeilen-Displays werden nicht unterstützt.

Closed 2020-10-05.

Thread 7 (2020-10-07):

It seems I am doing something wrong

goos766, 2020-10-07:
[errors.txt](https://github.com/ThomasHeb/4AxisFoamCutter/files/5337663/errors.txt)

goos766, 2020-10-07:
I tried to follow your description but it seems like I mixed up something. The Arduino IDE libraries for Windows are located in two places. Again, I don't understand what I'm doing wrong. I have replaced the U8G2 files in the scr folder. I have updated / downloaded the libraries you mentioned in the description. Then I realized there were two library locations so I swapped files in both folders. I guess somewhere I had to do more than I needed. I sent you the error list that the Arduino IDE generated. I'm not sure, but I think someone had a similar problem, only the conversation was conducted in German.

goos766, 2020-10-07:
[errors2.txt](https://github.com/ThomasHeb/4AxisFoamCutter/files/5337838/errors2.txt)
I tried again and got a similar result on a freshly installed Arduino IDE. With the procedure you recommend

goos766, 2020-10-07:
avrdude: stk500v2_receivemessage(): timeout avrdude: ser_send(): write error: sorry no info avail avrdude: stk500_send(): failed to send command to serial port avrdude: ser_recv(): read error: the handle is invalid.

I found this thread in German that I mentioned earlier. The file verification was successful, but unfortunately I got the above error at the end.

goos766, 2020-10-07:
[http://www.wch.cn/download/CH341SER_EXE.html](url) This file solved my usb 3.0 communication problems on Windows 10 with the Chinese Arduino Mega board. This is much more of a complication than with the 3D printer setup, and it would seem that the device is much simpler.

ThomasHeb, 2020-10-07:
Hi Goos!

sorry for my late reply... seems that we are working in different time zones ;o)

It seems, that you are linking the arduino.h. This header is a standard managing all background tasks.... and this is not compatible with the grbl. I think the SdFat brings the arduino.h back to the linker. Your errors are showing some linked files that are not included in the version I used.
Please use SdFat by Bill Greiman, **Version 1.2.3.**

Or use this libs https://github.com/ThomasHeb/4AxisFoamCutter/tree/master/03_Firmware/libraries

Only the file u8g2_font.c is missing (path /libraries/U8g2/src/clib/), due to > 25MB.

close the Arduino IDE.
save u8g2_font.c from your lib folder
delete the libs in your lib folder
copy the libs from the link above.
add u8g2_font.c under /libraries/U8g2/src/clib/
Start Arduino IDE and compile Foamcutter.

Closed 2020-10-07.

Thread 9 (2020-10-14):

SketchUp Foamcutter.rb does not generate GCODE as shown

ThomasHeb, 2020-10-14:
From youtube.com

After I select the paths, I am not getting the GCODE window to pop up like yours does at 5:49  Any idea why???

Please send me your SketchUp file for a deeper analysis.

Regards
Thomas

CWO4, 2020-10-14:
Here is the file requested.  Very simple cut going from square to round.  It is on the same SketchUp file you included as an example.  And also, the "Tower" gcode you included is not running correctly either.  The code actually runs and cuts, but the shapes are all wrong.

[Tower.zip](https://github.com/ThomasHeb/4AxisFoamCutter/files/5380110/Tower.zip)

CWO4, 2020-10-14:
Here is a photo of the shape that results from the gcode that is produced.

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

ThomasHeb, 2020-10-14:
thank you. I will check the code on my machine tomorrow.
was your machine already parametrized and did you made some successful cuts before?

the cut out looks a bit like axis-traveling for x and y is not ok and positioning of the foam is not correct. but this can also be an issue due to missing post process (square to round is a complex shape and needs a post process to calculate axis traveling from block shape, I will include some pictures tomorrow for better understanding)

CWO4, 2020-10-14:
Yes, my machine is working perfectly.  I built the one posted by RCKeith on
YouTube (Keith Howlett) and it has been producing perfect wings.  I just
wanted a way to get fuselage sections cut and I really like SketchUp.
SketchUp can generate .stl files for my 3D printing, but no GCODE.

Tom

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

ThomasHeb, 2020-10-15:
Hi Tom,
using SketchUp for fuselage is exactly what I do.
Your design is correct, you only missed the post process. Sketchup/Foamcutter.rb exports the two paths (left and right side) of the shape. If you do not run a post process, the foamcutter takes these patches as the machine movement. see picture below. if you add a foam somewhere in the middle, you get something between square and round.
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
What is a bit strange on your photos.... the width and hight of the cutout looks different..... these should be equal.
I made a small video showing the steps and insides.
Actually this doesn't help you, because my post processor is running on MacOS. But what I can offer is to extend the foamcutter.rb-tool with a basic post processor... but this will take some time and testing
[postprocess.mov.zip](https://github.com/ThomasHeb/4AxisFoamCutter/files/5382605/postprocess.mov.zip)

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

CWO4, 2020-10-15:
Thanks for the clarification.

I am very sorry this can't be used on a Windows machine.  Too bad the
software is not Java based (or other cross platform capable software) as
there are a LOT of Windows users out there that would actually pay you for
a program to do this since SketchUp has no other plugins that will do the
job.

I will have to look elsewhere I guess.

Thanks again,

Tom

PS:  You should add a note on your YouTube videos that this only works on a
Mac.  Will save a lot of wasted time for people using Windows.

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

ThomasHeb, 2020-10-15:
Tom,
stay tuned. the first SketchUp post processor is working.... I will post a demo here and hope you can support me for testing.

P.S.: Maybe someone could use my source and port it to Java.

ThomasHeb, 2020-10-15:
Hi Tom,

appending you find the foamcutter_V002.rb file. Please open SketchUp, the Ruby Code Editor and load this rb file and execute it. you will find a new menu "Foam Cutter Tool PP"
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

I modified your example (attached tower.skp.zip).
you have to add your machine dimensions at (1) and (4). the distance in between is the the distance between your axis (I added my machine dimensions).
The shape is placed in between and is equals the position of the foam inside the machine and the thickness of the foam (distance between (2) and (3)).
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

Select the Foamcutter Tool PP. Select
- (1) left machine side
- (2) left shape side (be careful to use the correct line)
- (3) right shape side (be careful to use the correct line)
- (4) richt machine side

The tool calculates the movement of the axis, draws the movements inside SketchUp. exports the Gcode, including hotwire on/of, power setting and feed sped (see foamcutter settings menu).
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
As you can see, my machine is too small to produce this shape.... I would need to reduce the machine width.

[default.gcode.zip](https://github.com/ThomasHeb/4AxisFoamCutter/files/5387030/default.gcode.zip)
[foamcutter_V002.rb.zip](https://github.com/ThomasHeb/4AxisFoamCutter/files/5387031/foamcutter_V002.rb.zip)
[Tower.skp.zip](https://github.com/ThomasHeb/4AxisFoamCutter/files/5387032/Tower.skp.zip)

Can you please test this... of course you need to modify to your machine dimensions.

Regards
Thomas

CWO4, 2020-10-15:
That looks REALLY nice!  I will test it tonight.

Tom

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

CWO4, 2020-10-15:
I am enclosing the SketchUp file modified to show my part and my machine's
dimensions.

Part placement is apparently critical.  However, I did manage to gee a good
part after a couple of tries.

This was only my first attempt tonight.  I will try more tomorrow.

Thanks again,

Tom

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

ThomasHeb, 2020-10-16:
Hi Tom,

Thanks for the first feedback. Not everything is possible inside a simple script compared to 3D calculation in Swift, but if you have ideas and wishes, let me know!

I had several problems on my fuselage, too. the small segments have a width of 60mm and behind the wing a big difference between the left and the right shape paths, so my axis movements have been too small. I reduced operational width of the machine from 721 to 350mm and for the nose to 200mm, so I could use full axis movement to produce big angles between the axis. The nose had 2 outer and two inner cut-outs per side, which I combined in my post processor and checked visual, if the hotwire is not intersecting the final piece.

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

I tried to rebuild that in the SketchUp PP Tool and this is not possible in a single calculation. But you can calculate the 4 cutting steps separate and then copy the relevant parts from the gcode together to one big file...

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

ThomasHeb, 2021-02-03:
foamcutter.rb with integrated post processor is released

Closed 2021-02-03.

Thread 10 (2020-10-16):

Code is not running

LarsBrinck, 2020-10-16:
Hi Thomas,
AFter succesful uploading...nothing happens. Having verified the hardware setup using the rrd-glcd-test (found here on github)  I´m quite lost. Screen background lights up but nothing happens. I can´t communicate through the serial monitor (?,§,! etc) - no response. I´ve tried to insert some Serial.print lines, buzzer etc in the code to get some idea of where the code stucks but no luck. (I have put 4 jumpers on X-/X+/Y-/Y+ and disabled limit switches and buttons in the config.h)

Any idea of how to debug or to pin down the problem?

ThomasHeb, 2020-10-16:
Hi Lars,

the board must open the display and show a welcome screen and wait for a button/jog... or go to an error screen (limit switch or estop).... but it must show something and communication must work in the welcome screen.... i tested this two days ago with arduino / ramps / display and no other hardware and no modifications on the ramps.
What board/arduino do you have?
What size of code did you have?
ROM 65586 Byte / 25%, RAM 5788 / 70%

I am a bit worried, that still some conflict with the libraries exist...

Appending a hex file, check out xloader for direct download
https://www.hobbytronics.co.uk/arduino-xloader

Regards
Thomas

[FoamCutter.hex.zip](https://github.com/ThomasHeb/4AxisFoamCutter/files/5392270/FoamCutter.hex.zip)

LarsBrinck, 2020-10-16:
I´m off to work right now but can test this tomorrow night or the day after (sun). I have one cheap chinese arduino copy (12MHz!?) and one (expensive) original 16MHz arduino - I´ve tested both with same result.

I´ll be back as soon as I´ve tested.

Thanks for your help!
/Lars

ThomasHeb, 2020-10-16:
Hi Lars,

do you have some programming experience on arduino? Just asking from where I should start the test scripts.
which type of ramps are you using? a had no problems with the one I bought first, the second one did not work at all, until I found a cold soldering connection on a 12V pin from ramps to arduino.

Regards
Thomas

LarsBrinck, 2020-10-17:
I got some basic experience doing a midi controller on a teensy making code snippets to make endless encoders behave ok, but that´s all. In this project I have called in support from a more experienced friend :)

Code size: "Sketch uses 67348 bytes (26%) of program storage space. Maximum is 253952 bytes.
Global variables use 6071 bytes (74%) of dynamic memory, leaving 2121 bytes for local variables. Maximum is 8192 bytes."

I can´t see any manufacturing data on the ramps board - I bought it from banggood so it is probably a chinese copy. But if I upload the code to the arduino without the ramps board connected, I should be able to communicate with it through the serial monitor using grbl commands -or not?

Seems to me as the arduino gets "bricked"...

Regs,
/Lars

ThomasHeb, 2020-10-17:
Hi Lars,

yes, good idea. Disconnect the Ramps.
If your download is working without any error, you should be able to communicate....

ok, let's start from the beginning:
- open Arduino IDE
- goto File/Example/01. Basics/Blink
- a new ion file is opened... select this window.
- open menu tools and select board and processor Mega 2560
- select your com port
- open menu sketch/upload ... takes a second and you should get a "Done uploading."
- now the LED L should blink 1s on, 1s off

- goto File/Example/01. Basics/DigitalReadSerial
- a new ion file is opened... select this window.
//  - open menu tools and select board and processor Mega 2560
// - select your com port
- open menu sketch/upload ... takes a second and you should get a "Done uploading."
- open menu tools/serial monitor. select on the lower right corner 9600 baud
- you should see many "0"s scrolling downward.
- close that window

- open foamcutter.ino.
- open menu sketch/upload ... takes some second and you should get a "Done uploading."
// - open menu tools and select board and processor Mega 2560
// - select your com port
- open menu sketch/upload ... takes a second and you should get a "Done uploading."

- open foamcutter.ino.
- in config.h set
   #define USE_LIMIT_SWITCHES                1
   #define USE_BUTTONS                       1
- open menu sketch/upload ... takes some second and you should get a "Done uploading."
// - open menu tools and select board and processor Mega 2560
// - select your com port
- open menu sketch/upload ... takes a second and you should get a "Done uploading."
- open menu tools/serial monitor. select on the lower right corner 115200 baud
- press the reset button on the Arduino
- both LEDs on the Arduino should be on
- you should see in the serial monitor
   Foam Cutter: Mega2560 with 4 axes (X, Y, U, Z)
   Grbl 0.8c2 ['$' for help]
- type "$" in the input Boxand press Send, you should see the help
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
- close that window

If possible download the hex file from my last post to your arduino with loader

Regards
Thomas

fredrik-jacobsson, 2020-10-17:
Hi Thomas - thanks for your input!

Success with your hex-file and the XLoader. Both Arduinos run the code and I can communicate through the serial interface. Both Arduinos work with my Ramps board as far as the display is concerned. I haven´t tested with drivers and Steppers yet. (The endless encoder code really seems to be in need of rewriting but that is NOT the concern of this issue - I´ll be happy to see if my code can do the job later on:))

I had tried Blink and some other sketches to test the cards as a first check but it´s good to be sure :)

Still no luck uploading the code from my computers. (I´ve borrowed a PC since I get a avrdude:timeout() when I upload it from my Mac.) That code doesn´t work.

My guess is that you are right about the libraries and that I have conflicting libraries in the code I generate in my IDE. I switched over to this PC so the two imported Libraries are:
U8G2 ver. 2.27.6
SdFat_- Adafruit_Fork ver. 1.2.3

Perhaps it would be easier for me to start soldering buttons and install limit switches and run from your hex-file - but it seems so weird not to be able to see the actual uploaded code?

Any ideas where to go from here?

CHeers!
/Lars

LarsBrinck, 2020-10-17:
Thx for your input!

Success uploading the .hex file to both Arduinos. Grbl commands show up and both Arduinos makes the display run through my Ramps board so that seems to be working so far. (The endless encoder code needs rewriting but that is NOT the issue now. Lets see what we can do about that later:))

 I tried to upload code from the IDE of a PC that I have borrowed since my Mac gets this avrdude:timeout() error. No luck. That compiled code does not work. I think your guess that there are some conflicting libraries are right. This PC has U8G2 ver 2.27.6 installed and SdFat - Adafruit Fork ver 1.2.3 installed

Perhaps it would be easier for me to start soldering buttons and limit switches - but it seems strange not to see the actual code running?

Where do we go from here? I´ll try to attach drivers and steppers later tonight.

CHeers!
/Lars

ThomasHeb, 2020-10-18:
These are good news!
Nevertheless PC compiled source should work, too. Libs are correct.... so very strange....

Next steps are:
- add the buttons and LEDs to the Ramps. You can test them in the menu position
- calculate the steps per mm and set the microstepps according with the jumpers. Are you using belts?
- add the stepper driver to the Ramps.... maybe you set jumper over the limit switch pins on the ramps.
- adjust the driver https://www.makerguides.com/a4988-stepper-motor-driver-arduino-tutorial/ simply plug the stepperdriver in and measure/adjust the voltage over the resistor.
- connect 12V DC to Ramps 3/4
- add a stepper motor and test operation

Regards
Thomas

LarsBrinck, 2020-10-20:
Hi Thomas,
I thought I would make another attempt to compile the code on the PC. Two questions arise:
1 - In your folder "03_Firmware" there are the "libraries" folder with the two libraries "SdFat_-_Adafruit_Fork" and "U8g2". Apart from that (and the folder "Foamcutter")there is a folder named "Lib_8UG2" - is that folder or the files within needed anywhere?
2 - You mention in your  instructions that the "fonts.cpp"-file is missing in your U8G2 library and should be copy/pasted from another U8G2 library. But the "fonts.cpp"-file is not missing in your library? Is this of any significance i.e. should I download the U8G2a library and copy that "fonts.cpp"-file and replace the one in your U8G2 library?

Sorry for the confusion but I´m just trying to find out why your .hex file works and not your un-compiled files...

(I really don´t want to solder buttons...:))

/Lars

ThomasHeb, 2020-10-20:
Hi Lars,

in the folder 03_Firmware is
- Foamcutter: The Arduino source code
- Lib_8UG2: these two files are modified inside the 8UG2 Lib and need to replace the original ones
- library holds the libs (all files) from my Mac. Another guy got some problems with the linker, too, so I overed my versions of the libs. Only the file u8g2_fonts.c is missing on my git, because of file size. please copy this from your libsfolder. delete your libs folder, paste the one from here and add the u8g2_fonts.c

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

I think you want to wirk with a version w/o buttons. appending the hex file
[Archiv.zip](https://github.com/ThomasHeb/4AxisFoamCutter/files/5410125/Archiv.zip)

LarsBrinck, 2020-10-20:
Hi again,
Made an attempt on the PC and the results were not so uplifting:
With your U8G2 library it won´t compile - seems to be a font missing. With latest U8G2 library it compiles. And it compiles with both SdFat-Adafruit fork libraries, yours and 1.2.3.

BUT
I get the following errors in the compiling window:

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

and the arduino gets bricked.

SO
Would you like to compile a .hex file with buttons and limit switches set to 0 and I will try that?

OR
Just tell me to start soldering those (/&%€%& buttons :):):)

/Lars

ThomasHeb, 2020-10-20:
Hi Lars,

here we go.

[Limit0_Button0.zip](https://github.com/ThomasHeb/4AxisFoamCutter/files/5410142/Limit0_Button0.zip)
[Limit1_Button0.zip](https://github.com/ThomasHeb/4AxisFoamCutter/files/5410143/Limit1_Button0.zip)

the error above may result from the missing u8g2_fonts.c - see above.

LarsBrinck, 2020-10-20:
YES! It accepted the compiled code when I changed those two U8G2-files.
Plus - I can now change limits and buttons and it still compiles and the code is accepted.
When I set buttons to 0 the endless encoder started to work with the LCD screen.
Happy Happy!
Time to connect the steppers!
Thanks for your support!

ThomasHeb, 2020-10-21:
You are welcome!
Have fun with the project and happy cutting

Closed 2020-10-21.

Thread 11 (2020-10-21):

Z and U mismatch in GrBl settings

LarsBrinck, 2020-10-21:
Hi Thomas,
Finally managed to calibrate the machine. Some confusion arose when $2 (z, step/mm) and $3 (u, step/mm) are interchanged in my GrBl settings. So when I change value in $2 the u-stepper(right horisontal) gets changed and vice versa ($3 changes  the z-stepper right vertical). This is contrary to the description in GrBl settings.

Can you check if you have got the same issue? They have the same value so it is not obvious but since this is my first day with GrBl it took me a while to pin down what was wrong.

I´m having great fun! Time to load the first gcode!

/Lars

ThomasHeb, 2020-10-22:
Hi Lars,

thanks for that feedback. The error is inside the text for the parameter setting report.cpp
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

Update is uploaded and you can simply change the report.cpp in your source folder.

Thank you,
Thomas
[report.cpp.zip](https://github.com/ThomasHeb/4AxisFoamCutter/files/5420822/report.cpp.zip)

Closed 2020-10-22.

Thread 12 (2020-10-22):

Endless encoder fix?

LarsBrinck, 2020-10-22:
Hi Thomas,
I´m cutting with success! Very happy. But the endless encoder sucks...:) - but I can manage. But I used a small script for fixing this in another project (midicontroller to Lightning Software where I used a bunch of endless encoders.) I tried this script as it is on the reprap screen encoder and it works flawlessly. But I can´t implement it in the lcd.cpp sketch - my friend and I spent the afternoon thinking it would be easy but we just brick the encoder...

Try this script. If you could implement the script in lcd.cpp to get the encoder work properly I would be most happy. Again.

Still having fun,
/Lars
[Encoder_Test.ino.zip](https://github.com/ThomasHeb/4AxisFoamCutter/files/5424056/Encoder_Test.ino.zip)

There is a similar/same approach here: https://github.com/buxtronix/arduino/tree/master/libraries/Rotary

ThomasHeb, 2020-10-23:
Hi Lars,
thanks for the feedback. I need to check that out over the weekend. The gcode and motion controller is controlling the loop timing. due to that the encoding is a bit tricky. I hope that I find some time to adapt your hints over the weekend.

Regards
Thomas

ThomasHeb, 2020-10-24:
Hi Lars,

the Encoder_Test.ino didn't work at all, but the Rotary Library you linked is doing a perfect job! I merged this with the lcd.cpp. Could you please do some tests before I upload it for public use?

Please copy the library Rotary to your Library folder and use the attached lcd.cpp
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

[Archiv.zip](https://github.com/ThomasHeb/4AxisFoamCutter/files/5432620/Archiv.zip)

LarsBrinck, 2020-10-25:
Hi Thomas,
Works like a charm! Well done! I will now leave you alone for a while and start cutting some cores :) The cutter has all the functionality I need now - maybe I will attach the limit switches and a fan later on. BTW - there is a free 4-axis gcode program for wing profiles here: https://www.rcgroups.com/forums/showthread.php?3467209-WingWire-4-axis-gcode-freeware (by the same guy who shared the cutter I built on Thinggiverse). Again - BIG THANK YOU!!!

ThomasHeb, 2020-10-25:
Hi Lars,

you are welcome. Have a lot of fun with your cutter!

Regards,
Thomas

Closed 2020-10-25.

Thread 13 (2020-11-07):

speed diode question.

goos766, 2020-11-07:
At this stage I finished soldering all the buttons and started soldering the diodes. a small problem appeared, I do not know at what point / at what action on my part the "speed" diode should turn on. Pressing a button doesn't change anything. Would switch to the appropriate menu, affect the functioning of the button and the activation of the diode?

ThomasHeb, 2020-11-08:
Hi,
you need to go to Position menu.
Normal travel speed is the feed speed (app 100mm/min)
Pressing the speed button will toggle to seek speed (indicated by speed led). seek speed can be set in parameters over usb for faster traveling.

Regards
Thomas

Closed 2020-11-08.

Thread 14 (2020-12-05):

Compiled Firmware not working

ThomasHeb, 2020-12-05:
Request from youtube / Ugur Demirkan
https://www.youtube.com/watch?v=fht_X7mQ-qg&lc=UgyDhqStnxrQoc5TaMB4AaABAg.9Gsrt8Y3kGy9Gt05Y3vglM

Ugur:
I compiled the program I loaded it I put it in Lib_8UG2 library, but there is no screen, where is I making a mistake thanks

Thomas:
Hi Ugur, did you follow the steps I posted on github? which hardware are you using exactly (a picture would be great, especially showing the wires between the Ramps and the display)? have you tested the display with another program? If you agree, I would open an issue on github and try to figure out a solution? Regards Thomas

Ugur:
I have installed Repetier-Firmware and it works fine. But I am loading your firmware, there is nothing on the screen.
RAMPS 1.4 Mega 2560 LCD 12864 kit

Thomas:
many times there are bad soldered pins on the boards. but if the repetier firmware was running on the arduino/ramps/display, we need to go a bit deeper. I will open a github issue and start with some simple test programs. do you have experience with programming / writing code for arduino?

ThomasHeb, 2020-12-05:
Hi Ugur,

We start step by step, to ensure alle parts of hardware are working correct, all settings in the arduino IDE are good .... so maybe many steps seems to be annoying ... but it is much easier to start from a working point, than to track an error backward.

Test 1: Please open the Arduino IDE.
Set Arduino Mega and you Port in the Tools menu.
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

Open the Blink Example
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

Compile and Download to Arduino Mega (without Ramps Board)
you should see the LED closer to the power connection blinking
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
Is test 1 working?

Test 2: Disconnect from the Arduino from the USB and connect the Ramps board (no external Power is required, no stepper or display needs to be connected.... but if they are connected, there is no problem)
Reconnect to USB Port.
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
you should see the LED on the Ramps close to the Mosfets blinking.
Is test 2 working?

Test 3: Open Arduino IDE. Check Port in Tools Menu and compile and download the Blink Example.
you should get no errors and the LED should blink again. This shows, that the Ramps is not disturbing the USB communication. Working?

ugurdem19, 2020-12-05:
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
I don't think there is a problem with arduino and lcd, Repetier-Firmware works fine. but 4AxisFoamCutter-master is compiling firmware but it does not work. The screen is white.

ThomasHeb, 2020-12-05:
Hi Ugur,

if the screen is white (filled pixels) this indicates an issue with the lcd driver.

please do the test 3, so that the blink is running on the arduino.
connect the lcd display and power over usb. the backlight should be on, but all pixels should be off (not white). is that working?

ThomasHeb, 2020-12-05:
Download the source from GitHub. you should get something like this
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

copy from 4AxisFoamCutter-master/03_Firmware/libraries
SdFat_-_Adafruit_Fork and U8g2 to the libraries folder of your arduino installation

open the attached LCD_Test.ino, compile and run it. you should see a text blinking
[LCD_Test.zip](https://github.com/ThomasHeb/4AxisFoamCutter/files/5647078/LCD_Test.zip)
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

ugurdem19, 2020-12-05:
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
no proplems, blink foam cutter

ThomasHeb, 2020-12-05:
yeah!!!!
ok. let's do the next step.
open the FoamCutter.ino from here, compile it and run it. you should see a welcome screen
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

ugurdem19, 2020-12-05:
Where will I download this file? Can you give a link?

ThomasHeb, 2020-12-05:
FoumCutter.ino is the source code for Arduino. you find it in the download from GitHub in the folder
4AxisFoamCutter-master/03_Firmware/FoamCutter.
you can open it directly from this folder.
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

ugurdem19, 2020-12-05:
https://github.com/ThomasHeb/4AxisFoamCutter/tree/master/03_Firmware I downloaded this file but it doesn't work

ThomasHeb, 2020-12-05:
please compile it again. do you get any warnings or errors, does the download work?

ugurdem19, 2020-12-05:
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

It is downloading, installing but not working.

ThomasHeb, 2020-12-05:
this is strange.
have you deleted any old copy of the U8g2 from you arduino/libraries folder and only copied the one from her to that folder?

Another test is to upload a hex file directly.
Appending a hex file, check out xloader for direct download
https://www.hobbytronics.co.uk/arduino-xloader
[FoamCutter.hex.zip](https://github.com/ThomasHeb/4AxisFoamCutter/files/5647164/FoamCutter.hex.zip)

ugurdem19, 2020-12-05:
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

thank you very much for your help when i upload hex

ugurdem19, 2020-12-05:
After installing hexi, I noticed that it was giving the following errors but still loading
Arduino:1.8.12 (Windows 8.1), Kart:"Arduino Mega or Mega 2560, ATmega2560 (Mega 2560)"

In file included from C:\Users\www\Desktop\4AxisFoamCutter-master\03_Firmware\FoamCutter\FoamCutter.ino:34:0:

sketch\nuts_bolts.h:30:0: warning: "max" redefined

 #define max(a,b) (((a) > (b)) ? (a) : (b))

In file included from sketch\FoamCutter.ino.cpp:1:0:

C:\Program Files (x86)\Arduino\hardware\arduino\avr\cores\arduino/Arduino.h:93:0: note: this is the location of the previous definition

 #define max(a,b) ((a)>(b)?(a):(b))

In file included from C:\Users\www\Desktop\4AxisFoamCutter-master\03_Firmware\FoamCutter\FoamCutter.ino:34:0:

sketch\nuts_bolts.h:31:0: warning: "min" redefined

 #define min(a,b) (((a) < (b)) ? (a) : (b))

In file included from sketch\FoamCutter.ino.cpp:1:0:

C:\Program Files (x86)\Arduino\hardware\arduino\avr\cores\arduino/Arduino.h:92:0: note: this is the location of the previous definition

 #define min(a,b) ((a)<(b)?(a):(b))

In file included from C:\Users\www\Desktop\4AxisFoamCutter-master\03_Firmware\FoamCutter\FoamCutter.ino:34:0:

sketch\nuts_bolts.h:34:0: warning: "bit" redefined

 #define bit(n) (1 << n)

In file included from sketch\FoamCutter.ino.cpp:1:0:

C:\Program Files (x86)\Arduino\hardware\arduino\avr\cores\arduino/Arduino.h:124:0: note: this is the location of the previous definition

 #define bit(b) (1UL << (b))

In file included from C:\Program Files (x86)\Arduino\hardware\arduino\avr\libraries\SPI\src/SPI.h:17:0,

                 from sketch\limits.cpp:14:

C:\Program Files (x86)\Arduino\hardware\arduino\avr\cores\arduino/Arduino.h:92:0: warning: "min" redefined

 #define min(a,b) ((a)<(b)?(a):(b))

In file included from sketch\settings.h:34:0,

                 from sketch\limits.cpp:5:

sketch\nuts_bolts.h:31:0: note: this is the location of the previous definition

 #define min(a,b) (((a) < (b)) ? (a) : (b))

In file included from C:\Program Files (x86)\Arduino\hardware\arduino\avr\libraries\SPI\src/SPI.h:17:0,

                 from sketch\limits.cpp:14:

C:\Program Files (x86)\Arduino\hardware\arduino\avr\cores\arduino/Arduino.h:93:0: warning: "max" redefined

 #define max(a,b) ((a)>(b)?(a):(b))

In file included from sketch\settings.h:34:0,

                 from sketch\limits.cpp:5:

sketch\nuts_bolts.h:30:0: note: this is the location of the previous definition

 #define max(a,b) (((a) > (b)) ? (a) : (b))

In file included from C:\Program Files (x86)\Arduino\hardware\arduino\avr\libraries\SPI\src/SPI.h:17:0,

                 from sketch\limits.cpp:14:

C:\Program Files (x86)\Arduino\hardware\arduino\avr\cores\arduino/Arduino.h:124:0: warning: "bit" redefined

 #define bit(b) (1UL << (b))

In file included from sketch\settings.h:34:0,
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
ThomasHeb, 2020-12-10:
Hello Ugur,

sorry for my late reply, I was busy the last days.

You must copy the libraries from the GitHub download 4AxisFoamCutter-master/03_Firmware/libraries/ to your Arduino/libraries path, with is located on My Documents on Windows systems.

I did a test with a Windows system and Arduino 1.8.11. The code is working, but the power of the display after reconnecting to USB Power took 10 Seconds.... very strange.
With Arduino 1.8.10 on Mac, the display is available 1 or 2 seconds after reconnecting to USB Power....
Very Strange, maybe you can load a 1.8.10 version and test.

Appending you find the hex file for operation without buttons and without limit switches
[FoamCutter.ino.mega.hex.zip](https://github.com/ThomasHeb/4AxisFoamCutter/files/5672456/FoamCutter.ino.mega.hex.zip)

I would recommend, that you install at least limitswitches close to your 0;0/0;0 coordinates, so that you can perform a homing... automated traveling of all axis to that limit switches and then a defined bit forward to a defined zero-position.

ugurdem19, 2020-12-11:
I did everything you said before, I tried with different versions, I tried copying and replacing the library files you provided, all of them got an error code. Thank you very much for your interest. you are a very good person.

ThomasHeb, 2020-12-11:
Hope you can work with the hex-file. If you need any changes let me know, I can provide updates.

Regards
Thomas

ugurdem19, 2020-12-12:
I installed hex I have not installed the motors yet, after I tried it with the motor, I will install the old foam cutting cnc. How can I do motor step adjustment in the menu.
Thank you very much for your help. A great work. Also, how to convert gmfc files to dat file x y u z gmfc is very easy for me. I don't know jedi.

ThomasHeb, 2020-12-12:
Hi Ugur,

for changing the parameters inside the Arduino Firmware (grbl) you connect the Arduino Board to the USB. open Arduino IDE and open the Serial Monitor from the Arduino IDE/Tools menu.
Select a baud rate of 115200.
With the command $$ you can access the settings menu. to change a parameter simply type $x=y with x is the number of the parameter and y is the new value
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
see this video https://www.youtube.com/watch?v=Bbq8E3omgh8 or search for "grbl change settings"

I don't have any plan on GMFC. I use Winghelper for my wings and SketchUp for my fuselage. Currently I am working on a SketchUp Plugin to generate more complex gcode, including post processing. Sketchup is for free in an older version.

Please make a simple wing design, some screen shots and send me the GMFC file, or even better, check if you can find a export or gcode export and send me this file.

ugurdem19, 2020-12-12:
Thank you very much for your help, you thought everything very carefully. Do you have to work for rotary cutting?

ugurdem19, 2020-12-16:
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
I tried to install it again, it worked without any problems, I started translating the menu into Turkish. Thank you for your help

ThomasHeb, 2020-12-16:
Hello Ugur,

i have no background in rotary cutting or milling. I have some programming and hardware skills and started my career in research and development....  long time ago ;)

I am very happy, that you solved the problem. for translation you need to work in lcd.cpp only (and report.cpp only for parameter and messages on usb interface).

Please keep me updated on your project and let me know, if you need further support.

By the way, if you are still searching a software for drawing shapes and calculating the gcode, have a look at this topic https://github.com/ThomasHeb/4AxisFoamCutter/issues/9
You find a rb-skript in that post, which works for Sketchup and generated gcode directly. I am still working on some details and the video.... hope I get this ready over x-mas.

Regards
Thomas

ugurdem19, 2020-12-16:
https://www.youtube.com/watch?v=uWO8kMGxqGU
The other day I saw a video like this but I uploaded the dat file but it failed.

ThomasHeb, 2020-12-18:
This is a really cool Java program. it works quite well.
inside the gcode you should add some delays/pause for the hotwire to heat up.
At the beginning, change from
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
to:
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
You can do this with a text editor. Change the file extension to .gcode and you can use it.
A .dat-file is attached. check your the forum https://www.rcgroups.com/forums/showthread.php?3467209-WingWire-4-axis-gcode-freeware/page3

Another cool tool is here... online version
http://www.diyrcwings.com/app/
this guy made a perfect job. you only need to rename the exported file to .gcode extension
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
[Seling.dat.txt](https://github.com/ThomasHeb/4AxisFoamCutter/files/5717423/Seling.dat.txt)

Closed 2021-02-03.

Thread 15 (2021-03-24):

Help with Power Supply Choice

Kwadology, 2021-03-24:
Hi Thomas,

I've decided to build a 4axis foam cutter based on your project. I'm pretty handy at mechanical design but my electronics knowledge is lacking, (Limited mainly to building drones and planes) I've watched both your videos and RCKeiths, I have all of the electronic components that you mention apart from a power supply. I want to go the same path as you and use a single power supply, (I have a step down puck already). However, there is one element I don't quite understand before purchasing one. I know you are using a Lab supply and that the hotwire is powered via the Ramps 1.4 board and you can control the power output through your controls / software via PWM. My questions is where is the PWM signal being sent to? Does your Lab Supply have a PWM in to allow it to be controlled via this method or is the Voltage / Current from the lap supply constant and the Ramps board itself has the ability to control the power being output to the hotwire? (Presumably in that case up to a Max of whatever the lab supply is set to).
None of the power supplies I've looked at seem to have any kind of PWM input port that I can see. I'm looking at this one: https://www.amazon.co.uk/Variable-Eventek-Adjustable-Regulated-Alligator/dp/B07DQQBJF6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
However if the power is controlled by the Ramps board is there any advantage of having a variable power supply at all and would it be better to choose something like this https://www.amazon.co.uk/Surom-Universal-Regulated-Switching-Computer/dp/B071W121H7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
I'm planning on making quite a large cutter with probably 100cm - 120cm hotwire and will want to cut EPP foam so conscious I may need more power than cutting other types of foam, so want to make sure I have some headroom. Thanks in advance for any help / advice you can give.

SimonJohnCastle, 2021-03-24:
Interesting Question.
In my case I went for a 60V 5A bench supply as you need more voltage for longer wire lengths and I wanted to be sure.
If the output from the lab supply is fed through a PWM switching FET etc to further control the average power you can lock the
PSU into the wrong voltage and current limit, just to be aware if you observe this.

Kwadology, 2021-03-24:
Thanks very much for your reply, I wasn't aware about more voltage for longer length that's really useful. I'll have a look at some calculations to make sure I know roughly what I'll need.
So is there a pwm switching FET on the Ramps 1.4 board  or are you saying if I add one in somewhere? (I dont remember seeing this mentioned in the components list). I dont really see a need to be able to control the power through the Arduino control if I can do it through the lab supply, but conscious that if I'm using one power supply to power the hotwire with a step-down puck in parallel to power the Arduino, ramps, steppers etc. it will consume some of the power that i'll need to account for.
I guess what I was originally trying to ask as well, is that if the ramps has a switching get capable of controlling the power is there still a benefit of using a variable Lab style power supply like the one you mentioned vs a fixed output PSU?

SimonJohnCastle, 2021-03-24:
There is one on the ramps board, but it looks like its limited to 30V or 35V, I think Thomas mentions this some where.
You can always use an external FET if need be but then controlling the power needed at the right time in GCODE may be a bit tricky.
Better to just use the FET or Relay to simply turn the power on FULL and adjust it by hand on the PSU as needed.
You generally need to turn it up a bit a second or two once it enters the foam, to start with its too hot, then it cools in the foam, then you need more power

Kwadology, 2021-03-24:
Great, thanks for taking time to help with this. It sounds like 2 power supplies and controlling the hotwire power manually is the simplist way to go. Ill check out the power calculations for the wire and go from there.

ThomasHeb, 2021-03-24:
Hi Guys,

Thank you for sharing your knowledge and supporting each another. I would like to add some more information and offer further support.

The Ramps has a MOS FET on Board. When you use a Ramps Board 1.4 the MOSFET for the hotwire has an independent power connector. This means you can use one voltage level for the stepper and the Arduino and an other level for the hotwire. I strongly recommend to use a Ramps 1.4 Board. Using a Ramps 1.6 Board allows only one voltage level and you are limited to the maximum voltage for the Arduino (12V... max 17V) and you need do play with the thickness of your wire..... that's not the best way, because you want to keep the wire as thin as possible.

The on board MOS FET can operate up to 60V DC. The MOS FET is used to switch the hotwire on and off and to drive a PWM. I wrote up to 35V in the hardware section, but for the hotwire MOS FET, you can operate up to 60V DC. There are no limiting parts connected. I guess the 35V is coming from any capacitor limitation .... but not inside the hotwire part ... and sorry, I do not find the exact reason why I wrote 35V.... maybe too conservative.

Simon is on the right way. More voltage keeps the current low and the hotwire thin and allows longer hotwire length.
I am using a similar power supply with up to 30V... that fits perfect to my wire length.
have a look at https://github.com/ThomasHeb/4AxisFoamCutter/issues/5
PWM is finally only a kind of fine tune....

If you tell me the operation width of your machine, I can do a quick calculation for a thin wire. Best would be the length of the wire, when it is fully diagonal from lower left front to upper right back corner.

Using a buck converter (step down) is a kind of standard for my hardware - but not required. I want only one laboratory power supply... so i need to generate the 12V for Arduino/Stepper out of this supply, too. But It works fine, too, if you use a second power supply.

Best regards,
Thomas

Kwadology, 2021-03-26:
Hi Thomas,
Thanks so much for your comments that helps a lot, sorry its taken time to reply ive been deciding on final dimensions.  The hotwire will be 120cm, maybe 125cm between connections. (Max diagonal length).
I would definitely prefer to use only 1 power supply, I have a Ramps 1.4 board and already have a buck convertor although its only rated for 40v max so I may need another if I should choose a 60v rather than 30v power supply.
[£3.70 62% OFF]Geekcreit® DC 6-40V To 1.2-36V 300W 20A Constant Current Adjustable Buck Converter Step Down Module Board Module Board from Electronic Components & Supplies on banggood
https://banggood.app.link/5c1j5t8kWeb
If your able to suggest what wire I should start with and if 30v is okay or I should choose 60v, that would be an amazing help. I do want to cut epp foam which I know is pretty dense so ill definitely need a slow feed rate but I'm not sure if I'll also need more power. Thank you.

ThomasHeb, 2021-03-26:
Hi,

slow feed rate is always better than more power, because you must keep in mind, that one axis may travel slower than the other one, so higher power may case unwanted melts... have a look at the speed correction and the tower example video.
In this video, you can see how to setup the hotwire power for low cutting speed.
https://github.com/ThomasHeb/4AxisFoamCutter/files/5382446/IMG_4588.mov.zip

I would recommend this wire (I use it). It is thin 0,2mm, app 14 Ohm/foot or 46 Ohm/m. I am cutting XPS Foam... the yellow one from the video, this is similar to EPP.
https://www.amazon.de/Proxxon-28080-Ersatzschneiddraht-Thermocut-Rolle/dp/B0016ODWWC/ref=sr_1_5?__mk_de_DE=ÅMÅŽÕÑ&dchild=1&keywords=proxxon+heißdraht&qid=1616770703&s=diy&sr=1-5

Appending the calculation. I recommend a 60V DC Supply, because you need 42V minimum.
For normal operation I would start with 50V and adjust the hotwire power setting (see video above).
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

The Geekcreit® DC 6-40V won't work. you need to find a DC DC step down with input voltage up to 60V DC or take a separate supply for the arduino/stepper motors (output 12V DC... app 3 A rating. You will need app 1A in normal operation, enough reserve to work without cooling/fan for the supply).

Best Regards,
Thomas

Kwadology, 2021-03-26:
That's an amazing help, thank you so much. I'll order  a 60v lab supply and look for an appropriate step down buck convertor. I'm sure I'll have questions as I work through but your comments in issue 5 are also really helpful. Thanks again.

Kwadology, 2021-03-26:
Hi Thomas, sorry for another question.  Could I just check this is a suitable buck convertor. Maybe a silly question it says 60v to 12v up to 10A. I'm just surprised there is no heatsinks on it like the lower voltage ones.
https://www.amazon.co.uk/dp/B07DNHXWV5/ref=cm_sw_r_cp_apa_fabc_AA607BZ570A61PDADSBH?_encoding=UTF8&psc=1
Thanks

Kwadology, 2021-03-26:
Actually the reviews for that look bad. Maybe with the higher input voltage a 2nd power supply is a better idea.

ThomasHeb, 2021-03-27:
Hi,

the module should work, but you are right, the reviews do not look good.
I checked out some modules and it is hard to find something above 50V. I think the main limitations are capacitor voltage rating, linear regulator for chip supply and voltage rating of MOSFEET. If you have good knowledge in electronics, you can upgrade the parts. Otherwise I would recommend to buy a external supply.

Kwadology, 2021-03-28:
Thanks for highlighting that psu. Much cheaper than I thought. Thanks again for your help.

SimonJohnCastle, 2021-03-29:
I guess, you have solution by now, but I if not you could always use a boost converter for the high voltage.

Closed 2021-04-03.

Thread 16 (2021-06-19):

Creality Melzi Board V1.1.2 and compiler error

ThomasHeb, 2021-06-19:
Request from youtube:
Can I use it on the Creality Melzi Board V1.1.2?

https://www.google.com/url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

What do I need to modify it needed?

=========
Getting this error while compiling

lcd.cpp:1:10: fatal error: U8g2lib.h: No such file or directory
 #include <U8g2lib.h>
          ^~~~~~~~~~~
compilation terminated.
exit status 1
U8g2lib.h: No such file or directory

ThomasHeb, 2021-06-19:
To the Creality Melzi Board V1.1.2:
you need to work with a arduino mega compatible board. this means an atmeal ATmega2560 or compatible chip must be used and the pinout should be similar. you need to compare the circuit diagram of this board with the arduino mega 2560 board first.

To the compiler error:
you need to download the library from my githubfolder
Download the libraries directly from this github: /03_Firmware/libraries and store in your ../Arduino/libraries/ folder (prefered, because updates of the original libraries may cause problems with grbl)

browse for the u8g2lib.h. it should be in this folder.

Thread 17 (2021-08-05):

Some Questions by Neo

ThomasHeb, 2021-08-05:
Request from youtube
https://www.youtube.com/watch?v=WJ8nHyDqIhs&lc=Ugz1C6c4nUitd0avGOt4AaABAg
by Neo2001cro

I will try to break the questions in some related topics and explain them step by step. Please feel free to ask for further details

===================

Thomas thank you.
Your 'work', sharing knowledge, plans, pictures, scripts... is apsolute great, excelent! Respect. Thank you.

And if i can, have you 'dialed in' your Foam Cutter to the German precision ;)?
Do you have wire temperature under control, are the tolerances aceptable?
Can you please show some of the 'action' of the Foam Cutter and Laser Cutter? How many models have you make with it?
Your foam cutter can make shapes in what dimensions, for example, can your foam cutter make DLG wing, 750mm long, with 50mm (170mm)  airofil on one side, and the 25mm (90mm) on the other? (becose of the wire 'pitch', is there enough height in your foam cutter) ?

And, you have shared plans, but, wire tension sistem, holes in aluminium profiles, brackets... Can you please explain, show that little bit more, like, idiot proof ;) ?
Steper drivers, i bet that drivers works great, super, but ;) if you listen them for long time they become unpleasant, or am i wrong? Have you try, do you recomend some quieter drivers?
Ramps 1.6 is better then 1.4?...

Your laser cutter looking great to, but, please share some more videos, what have you succed to done, what have you not...

Again thank you and please make some more videos, upgrades... you are on the right path, respect.
IMHO your Foam Cutter and the Laser Cutter are on the right 'track' to become No.1 for the RC people! Please don't stop perfecting it.

I am sorry for my very bad eng :(

ThomasHeb, 2021-08-05:
**Foamcutter: Wire temperature / Dimensions:**

You can build the cutter as big or as small as you want. I have chosen the V2020 rails with NEMA stepper, because they are available on Banggood.com and only some modifications on the idler pulley are required. But they are oversized for that task. Google for rcKeith, this guy has a much more simpler mechanical construction.

What you should keep in mind:
X travel dimensions should be bigger than your wing depth: 170mm wing depth >>> min. 250mm operation depth
Y travel dimensions should be bigger than your wing height: 50mm wing height >>> min. 100mm operation height
because you will always need some foam surrounding your wing.

Wing span is related to the distance between the two axis pairs.
On one hand you should have some additional space...i.e 750mm (total span is 1,5m?!?) your operational distance should be 850mm. BUT if you have non parallel traveling (i.e. reducing wing depth on the outer tip), a big distance between the axis pairs will increase X and Y required. See pictures.
I would recommend, that you build the axis pairs moveable, by clamping them on a table, or adjusting them along a rail. My solution is not a good one!

https://www.youtube.com/watch?v=WJ8nHyDqIhs&lc=Ugz1C6c4nUitd0avGOt4AaABAg

ThomasHeb, 2021-08-05:
**Foamcutter: Wire temperature / accuracy / tolerances**

Most important thing is, that your axis are orthogonal.... 90°. Assuming this is mechanically adjusted, the tolerance is related to:
- tolerance in the mechanical travel system (belts,...) and the flexibility of this system (more flex, more worth). Cutting foam does not need much power/force... so belt driven systems are ok. If I really put pressure on my system, I can move it about 1mm.... but this is not realistic during cutting. it is important, that you reach the same point during back travel. try a screw to the right and then to the left, you will find some degree of turning, without in/out movement. screws can operate a lot of force, but get expensive when reducing this issue. I use a belt, because that issue is very small, if you tighten the belt. Belts can not operate a lot of force....but I don't need it ;o)
- Firmware. I use 80 micro steps per mm, so my max resolution is 0,0125mm... you need a high resolution to accelerate over the steps. so firmware is very accurate
- hotwire itself: if you melt a foam with a hotwire, you will see at least 0,5mm melting around the hotwire.... and THIS drives the accuracy! in Addition the thickness of the hotwire... use a thin one!

find the lowest temperature to cut the hotwire, by butting some foam on the hotwire and increase the power setting. see video in zip. Then do some test cuts with that power setting at certain speeds.... I do my cuts with 100mm/minute
[IMG_4588.mov.zip](https://github.com/ThomasHeb/4AxisFoamCutter/files/6937175/IMG_4588.mov.zip)

neo2001cro, 2021-08-05:
ThomasHeb thank you!
You are realy professional

From where to begin ;)
I have wish, desire to build that cutter, but, i wanna that is very precise, and that meets every RC builder dreams ;)
No presure at all on you ThomasHeb ;) :)
You say 1,5m!, yes, true, its big, but ThomasHeb, if you can make foam cutter that can 'perfectly' cut, in very tight tolerances, DLG wing, 2x750mm long, maybe even in one go, left and right like on "WingWire", you will literally become RC God!
You, and others will say that I'm exaggerating but belive me, that 'war', to simple build perfect DLG wing now is almost 30 years old :( (maybe even more).

ThomasHeb please make that true, become reallity.

DLG builder have become to that 'magic' number from years of experience (if i understod good), this 1,5m is excelent in air, and still easy to 'travel' with.
Now days, in 2021 there is a lot of 1m DLG that are really good, but, if you can cut 1,5m then you can cut it and 1m :)

You say that you see that "with sistem" on your cutter is not good, have you find better system?
Is, maybe, "DoDo Do" 'desing' is better, easyer, smarter... way to build?

And, i know, its much work, but what you tell to build somekind of "Parts list", that even people like me can, buy it, and build it, without much 'fuss'.

You say that combination of power, wire, 'components'... will always have some tollerances, so, can you make in your sketchup-cutter-tool-plugin option that will calculate, cut foam, in for example in 102% or even 98% of exact 'plans', like on 3d printer?

ThomasHeb, 2021-08-05:
Hello Neo,

Building a DLG is a combination of many tasks, like airfoil design, shape, weight, foam cutting, CFK, GFK, vacuum molding,.... and each of them on a very high level! and you need to understand the processes behind.

I can not give you a ready to rebuild part list for a cutter, which meets that accuracy without the technical understanding.

Example:
I have been measuring the cutting accuracy (0,6mm) and I add this in my SketchUp designs manually.
If I need to cut slower or faster, I know how much I have to add or subtract from my shape. This can be calculated in a software or a sketchup script, but this needs weeks or month of work and testing.  This is not worth for the 5 planes I want to build and I can not spend this effort on a hobby. I use standard functions in SketchUp instead, but I need to decide manually, If I need an accurate outer or inner shape is needed... Scaling a wing by 102% makes holes to 102%, too.... but 98% are required for holes.

If you are looking for professional tools you need to buy on industrial standard level. Way to expensive for me and my 5 planes.

WingWire or other tools generating or sending gcode will work with my machine, too. Never the less, from design to real wing are some big steps. Even if you look at the videos for wing wire [link](https://www.youtube.com/watch?v=uWO8kMGxqGU) you see, that the wire is melting a big portion of the foam. You need to find this issues and work through the optimisation process.

Regards
Thomas

ThomasHeb, 2021-08-05:
In addition a Lo100 made with the FoamCutter
If you look at the tailbone, you see some waves on the surface. It took me three attempts to get to this quality, but will need a lot more to get to a smooth surface. I sanded the surface, covered it with two layers GFK and usesd some filler... this is a no-go for weightoptimzed DLGs.

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

ThomasHeb, 2021-08-05:
Hi Neo,

sorry to disappoint you, the formula is much more complex and needs to do some shape and travel decisions, ...
But please keep in mind, that developing a good DLG ist much more than foam cutting. You need to know a lot about airfoils, geometrical or aerodynamical shrinking, aerodynamical effects, V-wing, arrowing, rudder primary and secondary effects, stability calculation ....
If you have a good design and if you understand what happens during normal flight from a theoretical  perspective, then generating the SketchUp model, adding the additional things for the cutter manually (wire diameter, ...) is less than 10% work.
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
neo2001cro, 2021-08-06:
Hi ThomasHeb
"str" file? You mean .stl?
I don't see it on my version :(

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

Profesional wing, from where do you get that :P
Why that i bother profesional with the beginer stuff :P
DLG guys cut that in 3 parts (for now, best way that i see is on hands with hand hot-wire, or very expensive CNC)

Gentlemen Jan-Henning i know ;) respect
For the gentlemen rcKeith i know to... he recomended you :P
IMHO your version of foam cutter is better...
I know little bit about Arduino, electronics, soldering...
But not even near like you do, **respect to you for your knowledge.**

Thank you for your 'research' on how to make very good DLG, i know that alredy, but maybe someone doesn't.

You have share, give, realy good base, maybe even to good!

But i wanna that finaly can be something done for 100% that even my kid can do it alone.
So why to solder pins, if there is no need to do that (that why i have asked for 1.6+ ramps board)
I know that 1.6 is not good like 1.4, but, bigthree have 'mantioned' something about improving 1.6, so sory for 'trying', asking for  **ramps 1.6+**
bundle soluutions, why not, even simplier, thumbs up!

About airfoils, hehe that is my area ;)
I can give you airfoils with that many 'dots' that you will tell me that i am nuts ;)
You se, that not bothering me ;)

ThomasHeb, 2021-08-06:
Hi Neo,

that is strange, I see the STL in SketchUpMake 2017. Maybe go to the warehouse (menu window/extension warehouse) and search for a plug in.
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

I think, we are coming close to the point.
Hotwire CNC is a complete project, with required knowledge about mechanics, electronics and arduino.
To design an airfoil or wing for CNC, you need to know how to use SketchUp or a CAD tool and you have to adjust the design to your CNC.

I did one wing with foam core and GFK mold. It took me 10x longer doing the design in CNC, building the machine compared to cut the foam core in a traditional way with alloy-rips manually. So CNC is worth to go, if you see it as an own project, or if you want to reproduce the wings in a high volume. It is a long way to get CNC that running 100%,  you must decide if it is worth for you to spend the effort and the research.

neo2001cro, 2021-08-06:
strange (about .stl) ...
about time, shure, we all must deside is it worth our time and money.
But, your Foam Cutter looks good in 'action' so, why not build something so good!
If you can, ThomasHeb please make even some more improvements, like i say allready to many times ;) you are the closest that i have seen on being on, cross, finish line to make perfect RC Foam Cutter.

ThomasHeb, 2021-08-06:
Thanks, that you like my cutter.
I can support you, if you don't get something running. But actually I don't have the time to do bigger improvements. The weather is getting better, we got our Cessna 172 and start travelling around a bit and the RC gliders want to fly, too ;o)

Regards Thomas

neo2001cro, 2021-08-07:
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

Oh man, that is so beatiful to hear, that shold be, that people enyoj in such a gret hobby, not that always 'build' something....

But ;) :P

When weather go bad, then, maybe ;) :P

Thank you THomasHeb for your work, its really really good!

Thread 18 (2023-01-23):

Update broke code...

LarsBrinck, 2023-01-23:
Hi Thomas, I´ve been cutting for some time with great result and your firmware has been working like a charm. Thanks! As I updated my setup with a new control-box I decided to implement limit switches and buttons as well (I´ve been using only the menu and SD-card/gcode to control the machine until now). When I updated the code - the machine went dead...

1. First I just took the old code and changed the "Set Limit Switch" and "Set Buttons" to 1. The code compiled and uploaded without errors but I got a blank screen. I checked the libraries (had been updated) and then reverted to the old libraries you have uploaded. Same result. No error but blank screen. I tried with and without the limitswitches plugged in and also with the -/GND switch inputs hard NC as I had my setup until now. Still just a blank screen. No sound from the stepper motors.
2. I then downloaded your updated firmware and got a compilation error: "DIOPIN_HOTWIRE_DDR" was not declared in this scope. I attach the full error code.

Do you have any clues or which way to go now? Are there settings in the new firmware code that I have missed? I use the Ramps 1.4 board. I don´t have any an or hotwire attached to the board.

[Error code Foamcutter 230123.txt](https://github.com/ThomasHeb/4AxisFoamCutter/files/10479292/Error.code.Foamcutter.230123.txt)

Cheers from freezing cold Sweden!

LarsBrinck, 2023-01-23:
As a last resort I rebooted my macbook and suddenly the code compiled and loaded. Very strange. Anyway, now it seems to work. Unfortunately I got so excited to test the limit switches so I started fiddling with my pliers in the Ramps board without disconnecting it from the mains. I shorted the + and - on the pins for the limitswitches. Something fried -f&#%k. Now the screen goes white when I run from the mains power. Powering through the USB still works so hopefully the arduino survived.

Feel free to close this issue - If you have any link to debugging a fried Ramps board I´ll be more than happy. I will order a new one today...

ThomasHeb, 2023-01-23:
Hello Lars,

nice to hear that you are able to do some cuts with that project!

Updating the source is manly for the laser cutter ;o) But I know, that the library's always make some troubles. Inside the great display and SD library, some resources are used, which cause a conflict with the timing of the CNC/stepper processing... mainly timer resources.
So every update of Arduino IDE may also update the libraries, too. And Mac is doing that worth... don't ask me why, I love my mac, but the Arduino IDE seems to be more stable on the Windows PC.

So process the following way:
Download the firmware / library from [4 Axis Foam Cutter](https://github.com/ThomasHeb/4AxisFoamCutter)
Install (Copy!) the libraries from /03_Firmware/libraries directly in your ../Arduino/libraries/ folder (prefered, because updates of the original libraries may cause problems with grbl)
You may delete other versions of this libraries first
Select the version FOAM_CUTTER in config.h file
Do your Settings
Compile and download.

I shorted + / - for sensors on may CNC shield, too. In the end it was only a fuse.
Do you have the chance to measure voltage with a multimeter?
If so, please check:
- 1st page in attached pdf: ramps: blue dot = GND, red dots should have your input voltage for the steppers. Normally F1 is damaged.
- 5V for display,.... is generated from the arduiono mega board. So as long as you drive from USB, USB powers 5V level (3rd page, green areas, lower one is a comparator which always switches to USB 5V is available.)
- to check: Programm the blink example on your mega (disconnected  from ramps). it should blink the onboard LED. disconnect usb and supply over the DC connector on the arduino mega. it should blink. you should have your input voltage on GND/VIN on the POWER header. and you should have 5V on the GND/5V on the POWER Header. if not, you blow up the voltage regulator IC1 on the arduino mega (see page 4).

Regards
Thomas

P.S. I possible, send some pictures of your machine and projects.

[Hints.pdf](https://github.com/ThomasHeb/4AxisFoamCutter/files/10481915/Hints.pdf)

LarsBrinck, 2023-01-24:
Hi Thomas - thanks so much for your reply. I was not looking forward to 10h of googling on "how to troubleshoot a ramps board" so I ordered a new on the fly from my local vendor - but getting this troubleshooting guide for the setup is just awesome - I´m very grateful!

So, analysis as per your instruction tells me that I´ve got 12.3V as input voltage on my steppers - does that mean that the Ramps board is ok?

Checking mega - it loads blink, works on USB, when I give it 9V from a battery I read 8.6V at the DC-input, 7.6 at gnd/vin and 6.6 at gnd/5V... so that means that I blew the voltage regulator IC1 on the mega?

If so - can I replace the IC1 or do I need a new mega?

I zipped some pics of my very simple setup (https://www.thingiverse.com/thing:3676825) and some of the airframes I´ve been cutting. Mostly slope wings that I vac-bag but the last one with the psycedelic pattern is compression moulded with foam cut cores. Building and flying/thrashing slope "planks" is my addiction :)

[Exportbilder.zip](https://github.com/ThomasHeb/4AxisFoamCutter/files/10492861/Exportbilder.zip)

ThomasHeb, 2023-01-24:
**So, analysis as per your instruction tells me that I´ve got 12.3V as input voltage on my steppers - does that mean that the Ramps board is ok?**
This means the fuse and the diode is ok. there may be a problem with some capacitor, but I would say the ramps is ok….. maybe
when powering the arduino with the USB cable and the ramps with 12V, can youmove the steppers within the menu POSITION? if yes, your ramps is ok.

**Checking mega - it loads blink, works on USB, when I give it 9V from a battery I read 8.6V at the DC-input, 7.6 at gnd/vin and 6.6 at gnd/5V... so that means that I blew the voltage regulator IC1 on the mega?**
his is a problem, the linear regulator must limit to 5V. you can change IC1, but there may be some other problems inside the voltage regulation part. I would propose to order a new mega board, too. Or get in touch with an electronic specialist, for checking all the components in around that area.

LarsBrinck, 2023-01-25:
I will borrow a new mega board today from a friend to see if it works. I will also try replacing the voltage regulator on the old one. If it doesn´t work I will just have to order a new one. Expensive hobby...

Thanks for all your help!

Regs,
/Lars

ThomasHeb, 2023-01-25:
I keep my fingers crossed, that only the regulator got hit.

Regards
Thomas

LarsBrinck, 2023-02-21:
Hi Thomas - got some time to dig into the foamcutter again and with the new borrowed mega and a new ramps-board it works again. All settings were gone but they were not that hard to restore in GRBL. So - doing job from SD-card works, homing works(!), so I can use the machine again. I´ve made some new wings  - tadaa!

Unfortunately there are some things that don´t work now and I would be happy if you could help me out:
1 - no buttons except the endless encoder works. Not even the "back" button on the display card. I´ve checked my new buttons and they short between ground and the different I/O pins according to the diagram in foamcutter.ino. USE_BUTTONS is set to 1
2 - the only menu-options that works are "Homing" and "SD-card". The other options does not work and since there is no "back" button you get stuck and have to reboot. In "Position" you can´t choose a position and go there - you can only choose "Set as home-position" and then you are stuck.

Is there any GRBL-setting that has to be set for the buttons to work. Do you think there can be something wrong with the display/reprap board? The "back" button itself works - I´ve checked it. And the display and encoder works.

Happy for all support!
/Lars

ThomasHeb, 2023-02-21:
Hi Lars,

with USE_Buttons = 1 the small knob on the display board is not used.

with USE_Buttons = 1, please boot to welcome screen, then connect D59 on ramps to gnd. this should move forward to main menue…. does that work?

Can you send me some pictures of the connection of the buttons on the ramps?

if you want, we can make a phone call tomorrow?
my email is thomas.heberlein@web.de, just send me your contact and a time proposal

regards
Thomas

LarsBrinck, 2023-02-22:
Hi Thomas,
Thanks for helping! I´m no electronics guy so perhaps I´ve misunderstood the wiring. Here is a pic of my test (I just made a breadboard hookup) and a sketch of my wiring.

To get from bootscreen to mainscreen I can press the encoder. I see that D49 is occupied by the reprap-board. How do I technically attach anything there? Solder on top of the reprap-board?

Perhaps we can talk somewhere at 18.00-20.00 tonight? I´ll email....
/Lars

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

ThomasHeb, 2023-02-22:
Hi Lars,

time is perfect.
the D59 pin on the ramps is the back button. the firmware allows skipping the welcome screen with all buttons. so you can test the ramps/wiring. I will send you a image of the wiring in half an hour.
wiring principle as shown in your picture is perfect.

Regards
Thomas

ThomasHeb, 2023-02-22:
[RAMPS 1.4 (RepRap Arduino MEGA Pololu Shield).pdf](https://github.com/ThomasHeb/4AxisFoamCutter/files/10801100/RAMPS.1.4.RepRap.Arduino.MEGA.Pololu.Shield.pdf)

you can connect the buttons directly on the ramps... find three examples attached.
to test the buttons, boot the device and press the button in the welcome screen. if the button works (edge detection) it should skip to the main menu.

LarsBrinck, 2023-02-22:
Tadaa! I think I got the logic of the button implementation now - they work in the position menu as the encoder did before in "no buttons" mode. I think that the "back" button in D59 solved it. Thanks!
I´ll jump right in to printing a new case with buttons. No telephone call needed right now.

Thanks for helping me out again!
/Lars

ThomasHeb, 2023-03-04:
solved

Closed 2023-03-04.

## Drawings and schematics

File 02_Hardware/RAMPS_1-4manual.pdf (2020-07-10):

# RAMPS 1.4 http://reprap.org/wiki/ramps

This is open hardware: you can redistribute it and/or modify it under the terms of the GNU General Public License as published by the Free Software Foundation, either version 3 of the License, or (at your option) any later version.

This hardware design is distributed in the hope that it will be useful, but WITHOUT ANY WARRANTY; without even the implied warranty of MERCHANTABILITY or FITNESS FOR A PARTICULAR PURPOSE. See the GNU General Public License for more details.

You should have received a copy of the GNU General Public License along with this program. If not, see <http://www.gnu.org/licenses/>.

!!! Reversing input power, and/or inserting stepper drivers incorrectly will destroy electronics and cause fire hazard!!!

Test all electronics thoroughly before placing into service.

Do not leave power supplied to electronics unattended, or run machines unattended due to the risk of fire and malfunction.

This is NOT a toy and it contains
small and sharp parts. Children can
choke or suffocate by swallowing small objects. Keep all parts away from children and never leave printer/parts unattended.

Bill of Materials
Qty Part Name | Value | Package
3 C1,C5,C8 | 10uF | 153CLV-0405
1 C2 | 100nF | C0805
6 C3,C4,C6,C7,C9,C10 | 100uF | 153CLV-0605
2 D1,D2 | 1N4004 | DO41-10
1 F1 | MFR500 | MFR500
1 F2 | MFR1100 | MFR1100
1 LED1 | green | CHIP-LED0805
3 LED2,LED3,LED4 | red | CHIP-LED0805
3 Q1,Q2,Q3 | STP55NF06L TO220BV
5 R1,R7,R11,R21,R22 | 4.7K (1%) | R0805
8 R2,R3,R4,R5,R6,R8,R9,R10100k | R0805
1 R12 | 1K | R0805
3 R23,R24,R26 | 1.8K | R0806
3 R13,R14,R15 | 10r | R0805
5 R16,R17,R18,R19,R20 | 10k | R0805
1 S1 | B3F-3100 | B3F-31XX
1 U$2 | 282837-6 | 282837-6
1 X4 | MSTBA4 | MSTBA4
1 | 0.1” 18x2 pin
8 | 0.1” 2x3 pin
5 | 0.1” 8x1 pin
2 | 0.1” 6x1 pin
6 | 0.1” 4x1 pin
2 | 0.1” 24x1 female
4 | 0.1” 8x1 female
15 | 0.1” 2 pin jumper

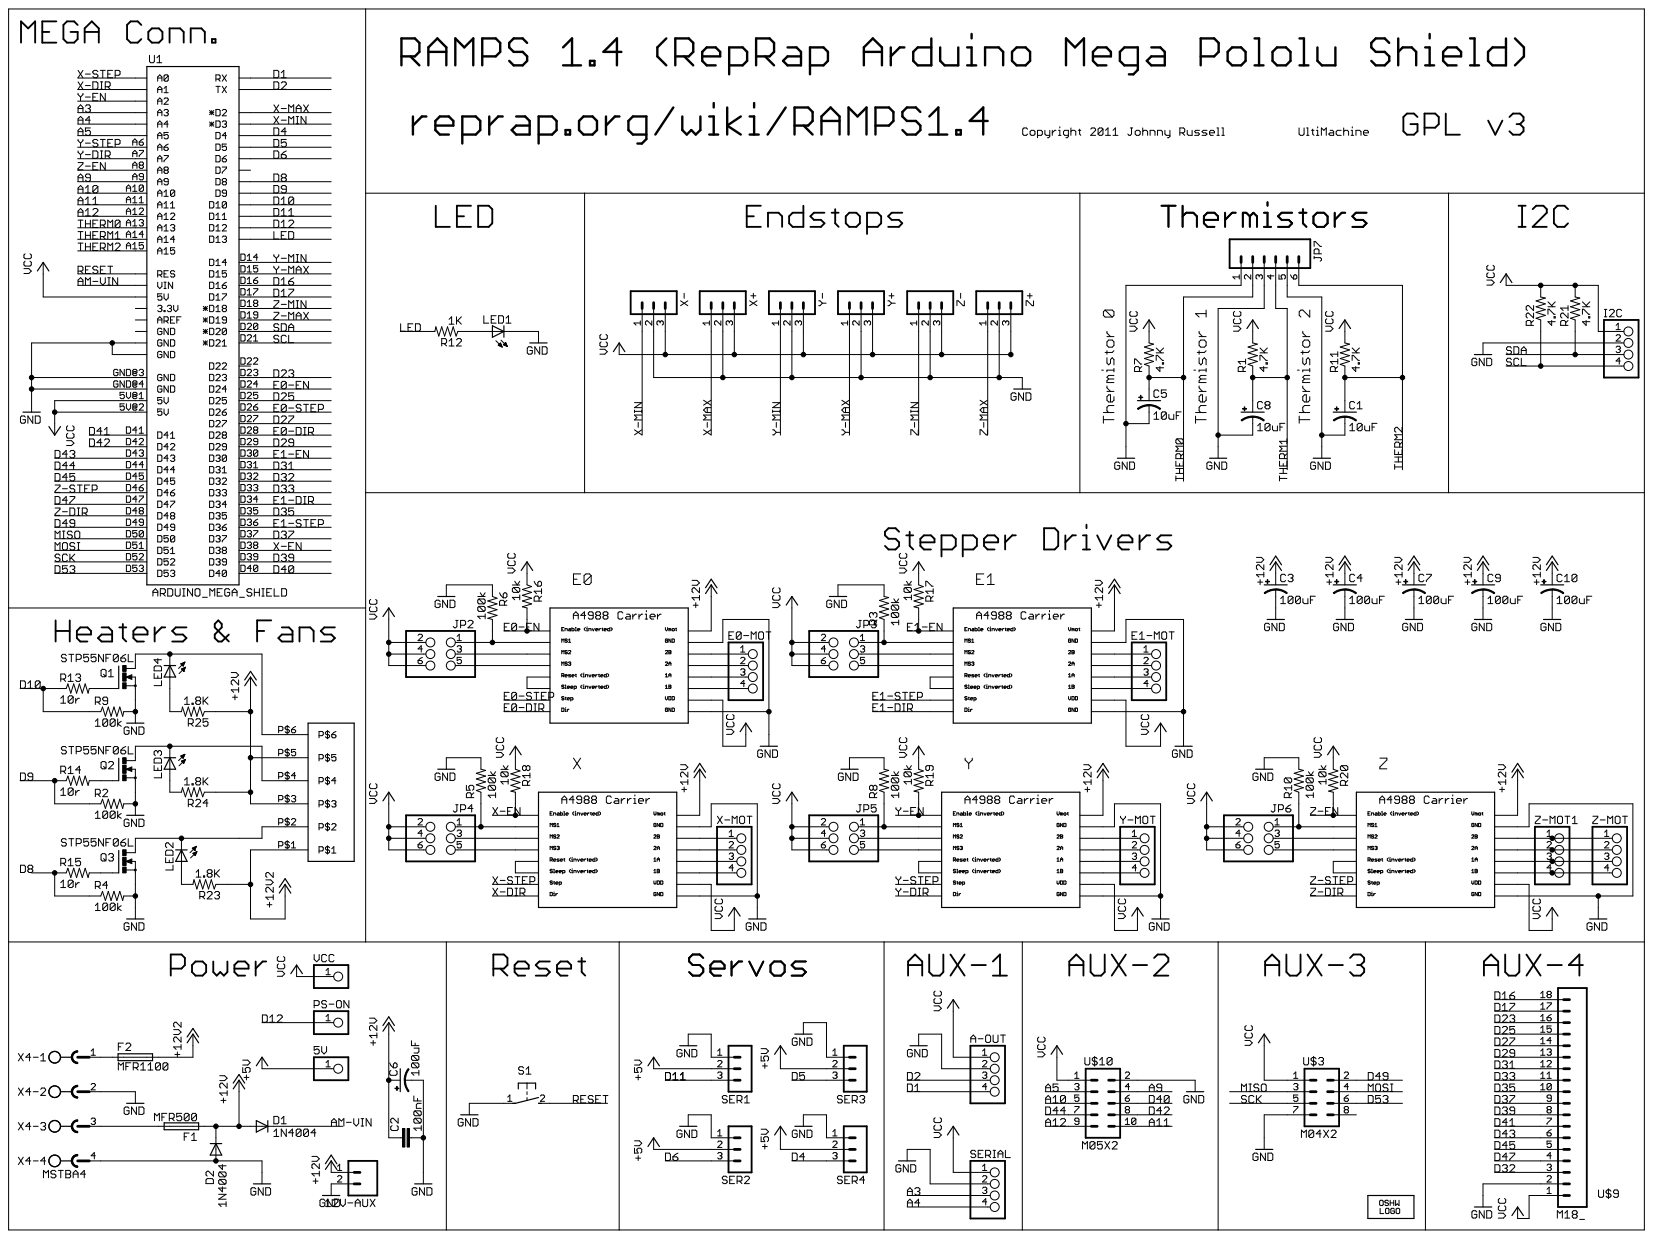
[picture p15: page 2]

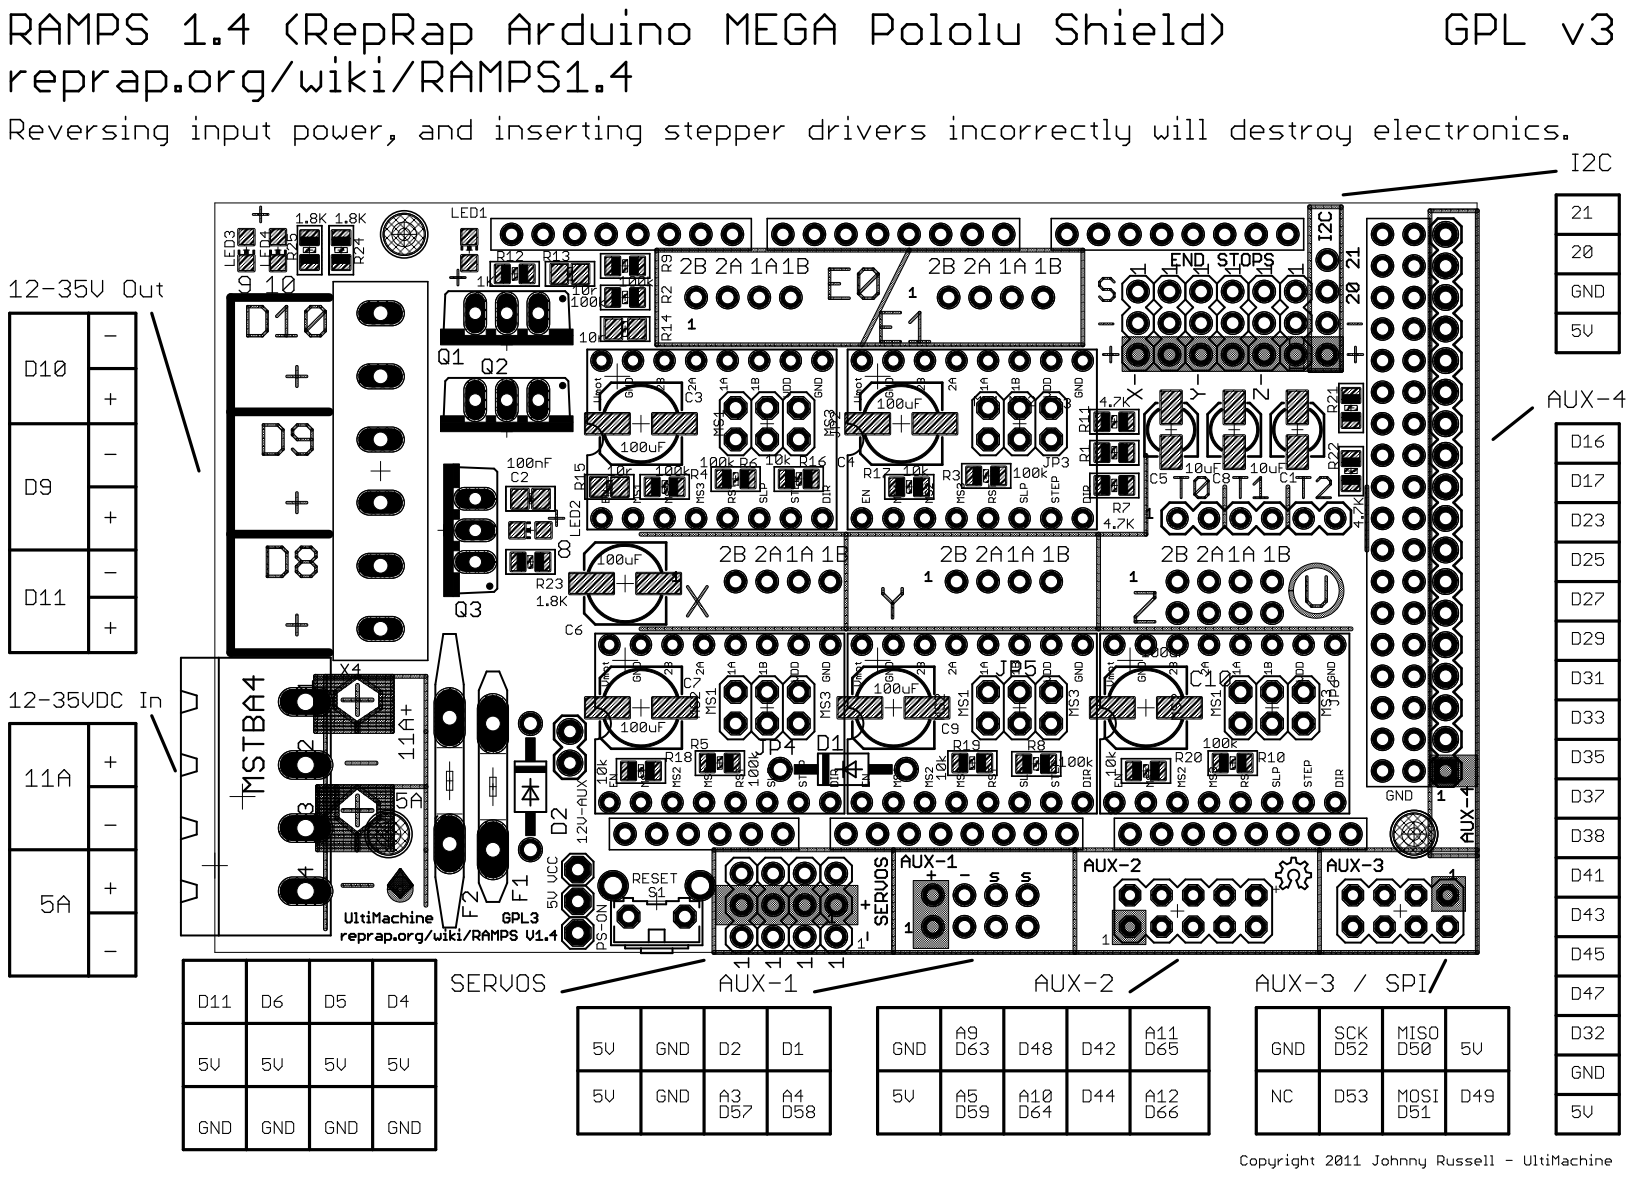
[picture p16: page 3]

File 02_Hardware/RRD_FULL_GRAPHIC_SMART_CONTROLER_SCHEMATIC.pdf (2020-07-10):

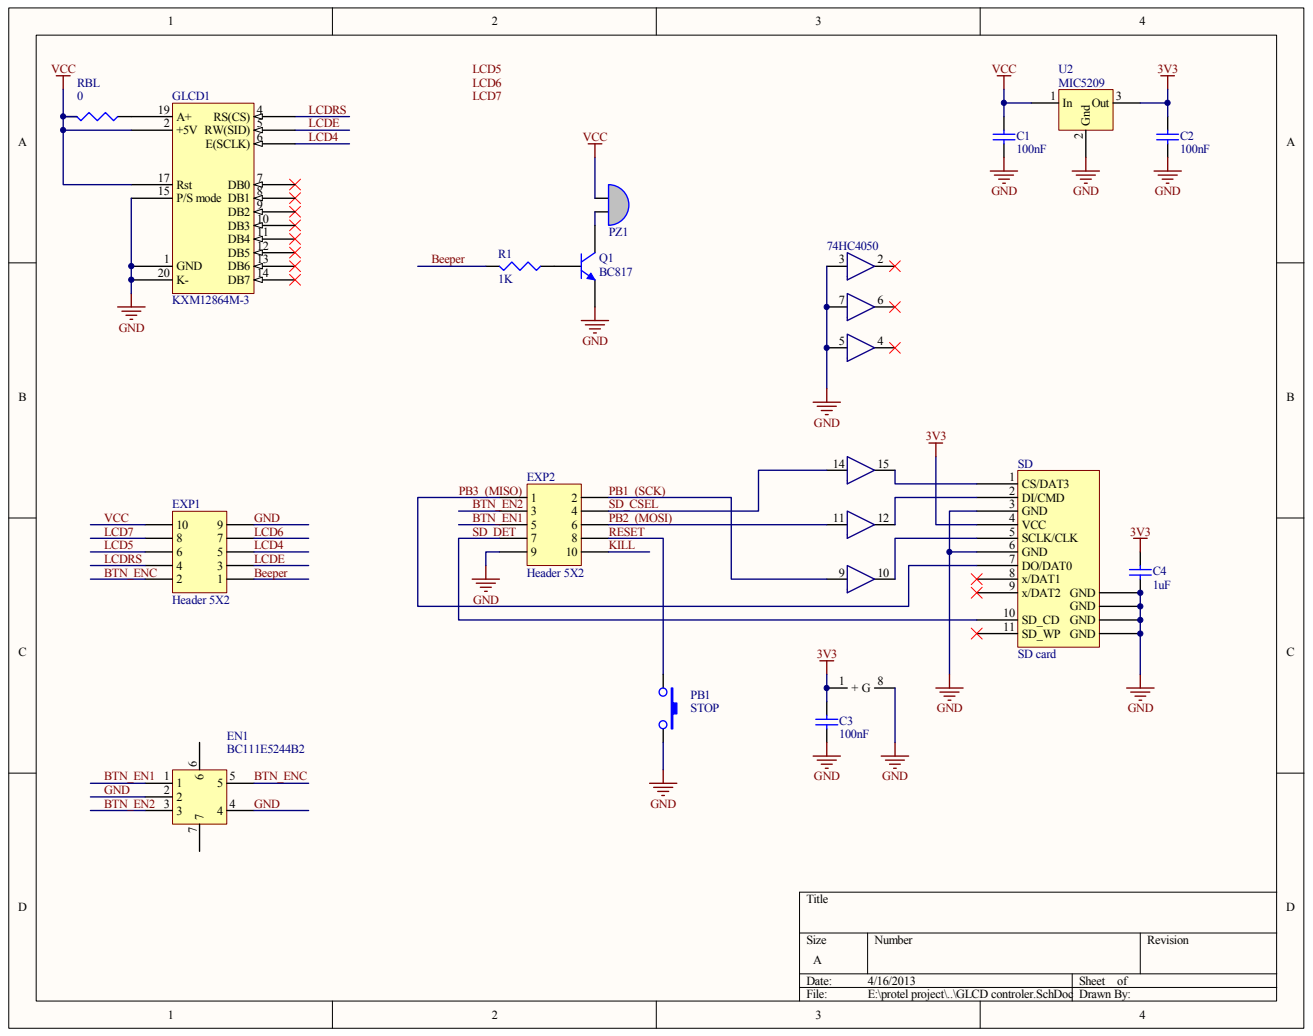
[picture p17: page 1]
Title; Size; Number; Revision; Date:; Sheet of; File:; E:\protel project\..\GLCD controler.SchDoc; Drawn By:; EXP1; Header 5X2; VCC LCD7 LCD5 LCDRS; GND LCD6 LCD4 LCDE Beeper; LCD4; LCD5 LCD6 LCD7; LCDE; LCDRS; GND; VCC; BTN_ENC; EXP2; BTN_EN2 BTN_EN1 SD_DET; SD_CSEL; PB3_(MISO); PB1_(SCK); PB2_(MOSI) RESET KILL; CS/DAT3 1 DI/CMD 2 GND 3 VCC 4 SCLK/CLK 5 GND 6 DO/DAT0 7 x/DAT1 8 x/DAT2 9; GND GND GND GND; SD card; Gnd; Out 3; U2 MIC5209; PB1 STOP; BTN_EN1; BTN_EN2; RS(CS) 4 RW(SID) 5 E(SCLK) 6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

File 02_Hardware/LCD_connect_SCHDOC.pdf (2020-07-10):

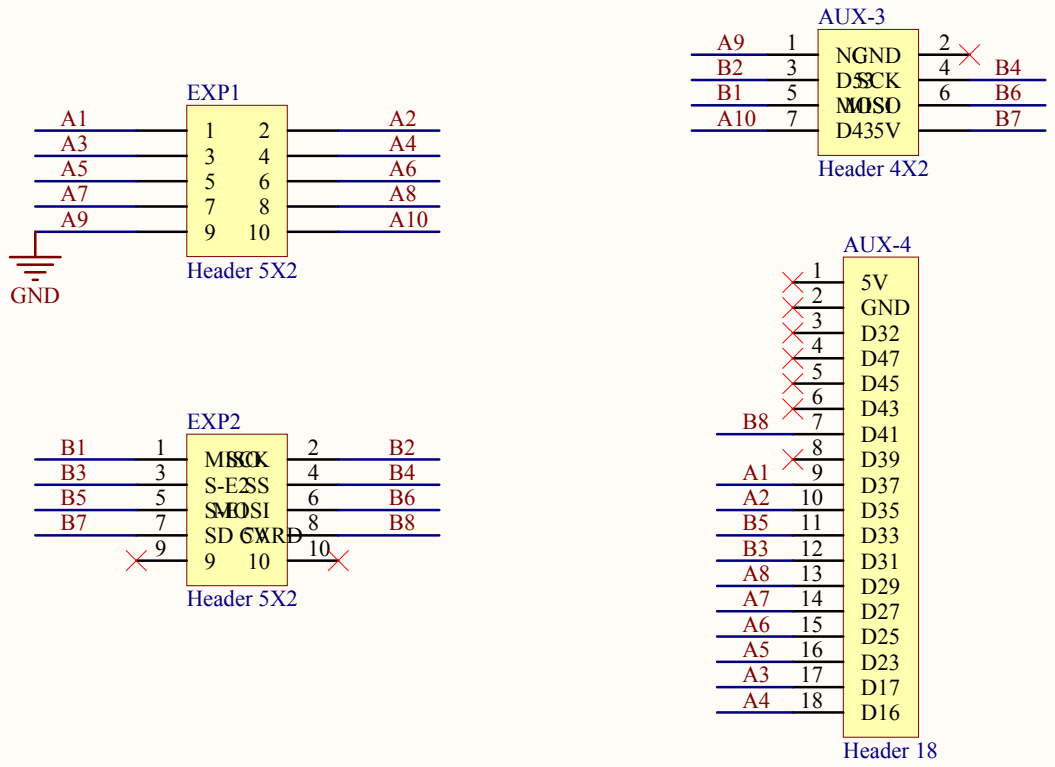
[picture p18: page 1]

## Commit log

2020-07-14 Optional disabling of limit switches and buttons
    For minimal hardware requirements, you can disable the limit switches and the buttons with two defines in config.h.
    in this mode homing is disabled and usability on display is adapted to operate only with jog and local button on display. No additional hardware is required.
2020-07-24 Add files via upload
    Store/load settings from registry
    Set camera to predefined poitions
    Import/export functions renamed
    Restructured Programm FCalc to App
    Simulation speed factor added
    Restructured in codable struct for load/save with json
    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
2020-08-18 Error correction and functional improvement
    Shape: Reverse shape added
    General: Merging after/before added
    Preview: Diameter of cutting lines as parameter
    General: Load optimized to use optional json decoding, to be compatible if value is not stored
    General: Handling of projectName optimized), callback if changed
    General: Statustext is generated and passed via callback
    General: horizontal/vertiacal mirroring added
    General: Error in travel speed with disabled speed optimization solved
    General: in case of speed calculation less then target speed, taget speed is used
    General: added comment for hotwire setting and foam material
2020-08-24 Rotation around w-axis added, minor corrections
    Import: Error on z-Axis for relativ import removed
    Import: Added additional gcode commands for import (read and ignored G17, G....)
    Import: order of read for one or two digit commands optimized
    Preview: reworked all update functions to improve speed for SCNNode update. Only relevant nodes are removed or recalculated
    General: Rotating shape around w axis
2020-09-11 New feature: Local speed change
    Speed change in positioning mode (jog) with local button between feed speed and homing seek speed.
    Selected homing seek speed is indicated with LED.
2020-10-18 Update README.md
    Added: Block diagrams for Ramps 1.4 and Ramps 1.6
    Marked: Cutting pin 10 is optional and not required if fans are not connected
    Added: Hotwire calculation and fine tuning
2020-10-18 Add files via upload
    Added comments regarding fan... only optional
    changed variable declaration position in lcd.cpp, according issue #8
2020-11-08 correction on speed selection for usage w/o buttons
2021-11-29 Update of gcode.cpp for laser cutting
    Laser cutting in Lightburn is controlled with G0 (seek, laser should be off) and G1 (laser is on) commands.
    G0 did not switch off the laser. gcode.cpp changed for seeking in laser-mode with laser off.
